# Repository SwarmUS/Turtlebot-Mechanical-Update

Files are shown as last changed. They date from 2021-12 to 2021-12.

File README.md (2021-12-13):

# Turtlebot-Mechanical-Update

This repository contains the 3D model of a modified Turtlebot Burger used by the SwarmUS project.

## Requirements
- Solidworks 2021

## Getting started

This repository contains submodule of 3D model parts. Right after cloning the project and prior to opening any assembly, run the following command:

```
git submodule update --init --recursive
```

### Repository structure

------

```
Turtlebot-Mechanical-Update
├── outputs
│   ├── dxf
|   ├── pdf
│   └── STL
|   	├── external
│   	└── internal
├── external
├── internal
├── TurtleBot
├── Turtlebot_modified.SLDASM
└── README.md
```

#### Turtlebot_modified.SLDASM

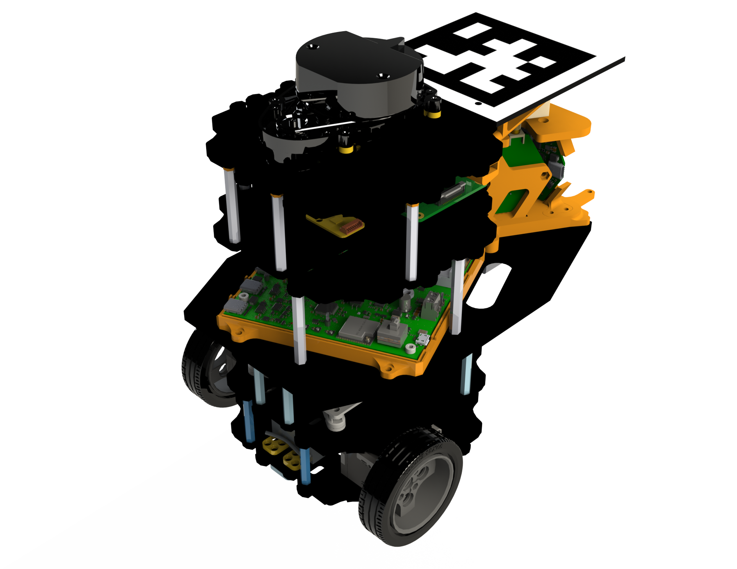
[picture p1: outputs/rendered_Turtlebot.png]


Main assembly of the modified Turtlebot. It's composed of a Turtlebot Burger with additionnal components that are external to the robot (*external*) and of components that are internal to the robot (*internal*). These components wrre mostly added to support mechanically and electrically the HiveBoard and its BeeBoards.

### Turtlebot

This folder contains all the components of the Turtlebot and it contains the Turtlebot's assembly itself. All the components and the assembly were exported from the Robotis Model on [OnShape](https://cad.onshape.com/documents/2586c4659ef3e7078e91168b/w/14abf4cb615429a14a2732cc/e/9ae9841864e78c02c4966c5e) and was converted to a SolidWorks assembly afterwards.

### external

Contains the 3D models of the external components and their supports. Significant assemblies and parts are described below:

- **qr_plate.SLDPRT**: Plate on which a QR code is glued on. Can be directly screwed on the Turtlebot top layer.
- **qr_plate_support.SLDPRT**: Supports of the qr_plate. The part has two [configurations](http://help.solidworks.com/2021/English/SolidWorks/sldworks/c_Configurations_Overview.htm), one for the port side and one for the starboard side.
- [HiveBoard-BeeBoard-Mechanical](https://github.com/SwarmUS/HiveBoard-BeeBoard-Mechanical): Submodule that contains the 3D models of the BeeBoard and the HiveBoard and their cases. 

### internal

Contains the 3D models of the internal components added to the Turtlebot. Significant assemblies and parts are described below:

- **REG_313080006.SLDPRT**: 313080006 5V regulator for powering the Hiveboard and its BeeBoards.
- **assembled_interloc_system.SLDASM**: Assembly of the HiveBoard, 3x BeeBoards, the voltage regulator (REG_313080006), a plate with the bolt pattern of all the components and some standoff for the assembly with the Turtlebot. The BeeBoards are placed in a specific pattern for interlocalisation.

### Outputs

- STL files of the custom made part in order to 3D print them.
- DXF files of the custom 2D plate. A .swg and a .pdf was generated for each .dxf files with 0.001" paths with the colorRGB(255, 0, 0) . This can be used with a laser cutting machine.

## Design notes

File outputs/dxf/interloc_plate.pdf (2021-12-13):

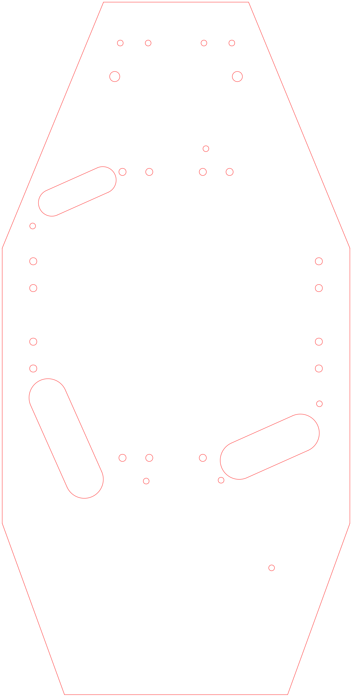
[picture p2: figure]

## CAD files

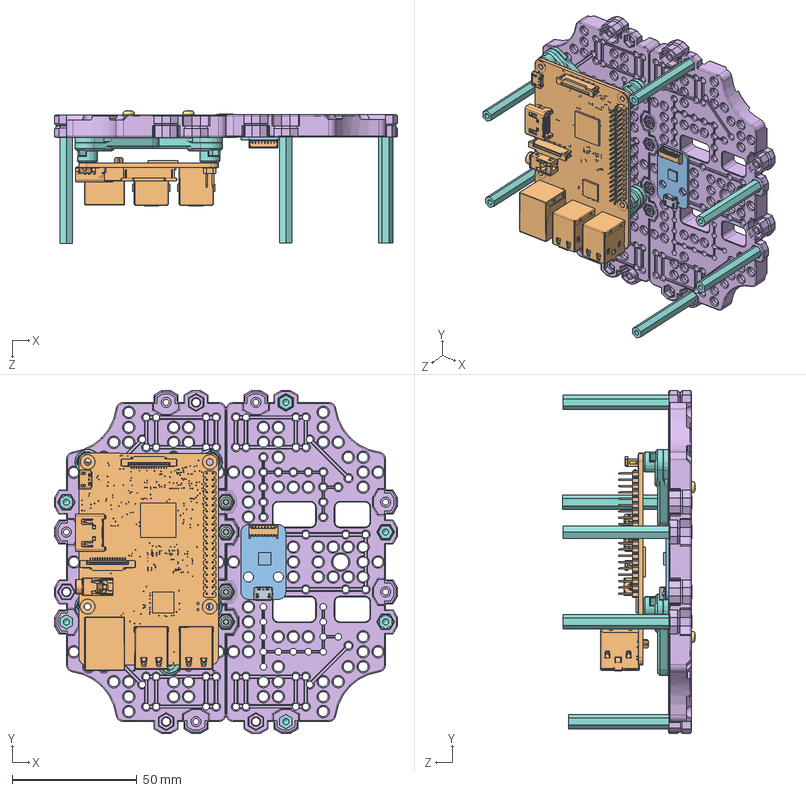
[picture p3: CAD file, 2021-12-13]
Turtlebot/Third Floor _1_.SLDASM
137.5 x 137.6 x 53.2 mm
MICRO_USB
BIC04_C01_PCB
PHS_M3X6 x 4
NUT2_M3 x 4
P-BP-A001_3D x 2
PHS_M2_5X12 x 4
PR30_IBB_01_3D x 4
Surface 18
Surface 28
Surface 36
Surface 25
Surface 34
Surface 11
Surface 24
Surface 26
Surface 33
Surface 31
Surface 1
SUPPORT_HEX_M3_0XL45_FF x 6
Surface 17
Surface 6
Surface 16
Surface 29
Surface 14
Surface 9
Surface 19
Surface 23
Surface 12
Surface 4
Surface 8
Surface 22
Surface 7
Surface 10
Surface 37
Surface 3
Surface 27
Surface 30
Surface 5
Surface 15
Surface 32
Surface 13
Surface 20
Surface 2
Surface 35
Surface 21

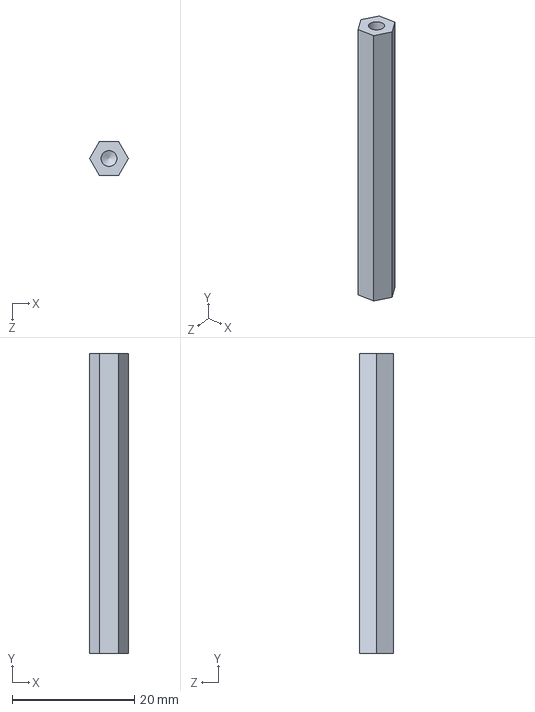
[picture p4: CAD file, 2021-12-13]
internal/m3_standoff_49mm.SLDPRT
6.35 x 49.0 x 5.50 mm

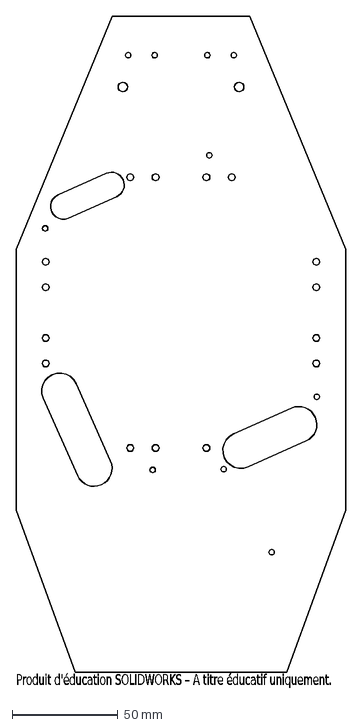
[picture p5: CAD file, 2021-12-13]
outputs/dxf/interloc_plate.DXF
Produit d'éducation SOLIDWORKS – A titre éducatif uniquement.

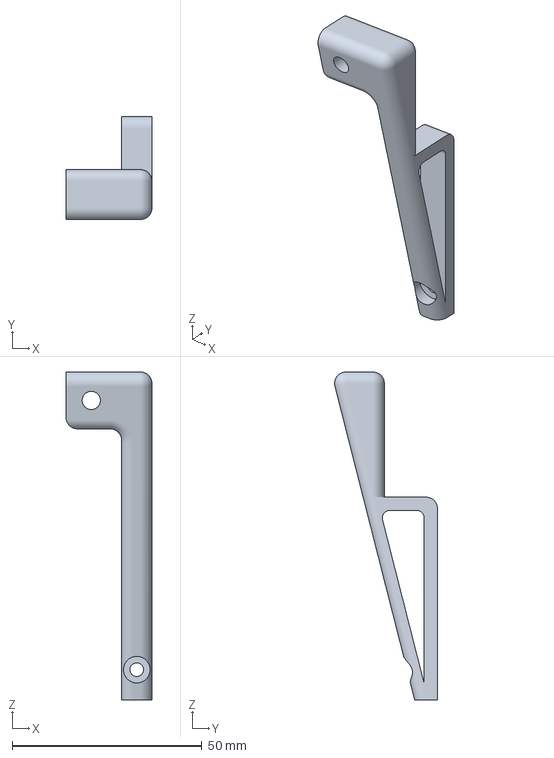
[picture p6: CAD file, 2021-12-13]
outputs/stl/qr_plate_support_miror.3MF
22.7 x 27.1 x 86.5 mm

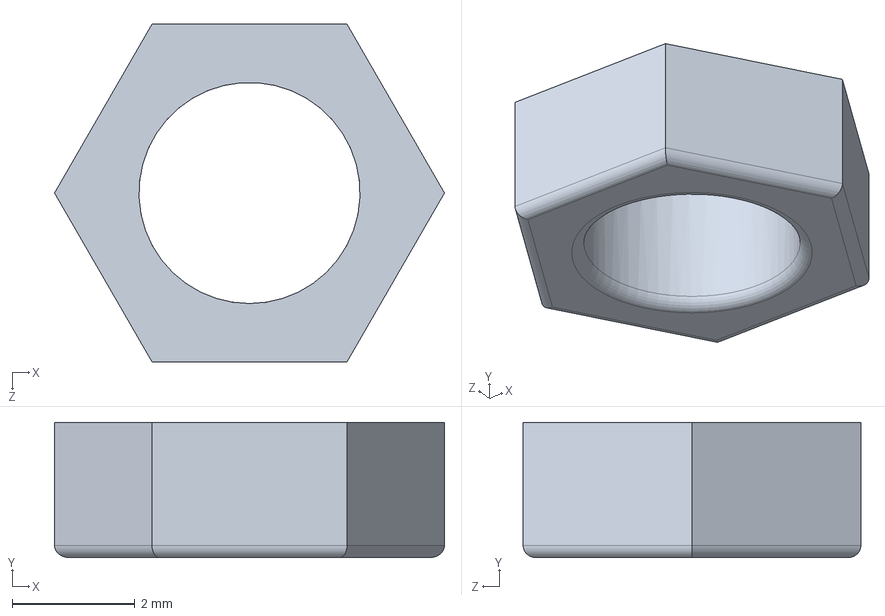
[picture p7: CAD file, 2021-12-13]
internal/hex_spacer_2_2mm.SLDPRT
6.35 x 2.20 x 5.50 mm

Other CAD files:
Turtlebot/wheel _1_.SLDASM
Turtlebot/OPENCR _1_.SLDASM
Turtlebot/connected plates _1_-3.SLDASM
Turtlebot/First Floor _1_.SLDASM
Turtlebot/Second Floor _1_.SLDASM
Turtlebot/connected plates _1_.SLDASM
Turtlebot/LDS _1_.SLDASM
Turtlebot/Forth Floor _1_.SLDASM
Turtlebot/ball_caster _1_.SLDASM
Turtlebot/wheel _2_.SLDASM
Turtlebot/USB2LDS _1_.SLDASM
Turtlebot/connected plates _1_-1.SLDASM
Turtlebot/connected plates _1_-2.SLDASM
Turtlebot/022035025.SLDPRT
Turtlebot/1-33154.SLDPRT
Turtlebot/1-33162.SLDPRT
Turtlebot/1-33193.SLDPRT
Turtlebot/1-33242.SLDPRT
Turtlebot/2-33160.SLDPRT
Turtlebot/2-33170.SLDPRT
Turtlebot/2-33199.SLDPRT
Turtlebot/2-33247.SLDPRT
Turtlebot/3-33158.SLDPRT
Turtlebot/3-33166.SLDPRT
Turtlebot/3-33196.SLDPRT
Turtlebot/3-33245.SLDPRT
Turtlebot/4-33155.SLDPRT
Turtlebot/4-33164.SLDPRT
Turtlebot/4-33194.SLDPRT
Turtlebot/4-33243.SLDPRT
Turtlebot/50MIL_HEADER_BODY-33149.SLDPRT
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

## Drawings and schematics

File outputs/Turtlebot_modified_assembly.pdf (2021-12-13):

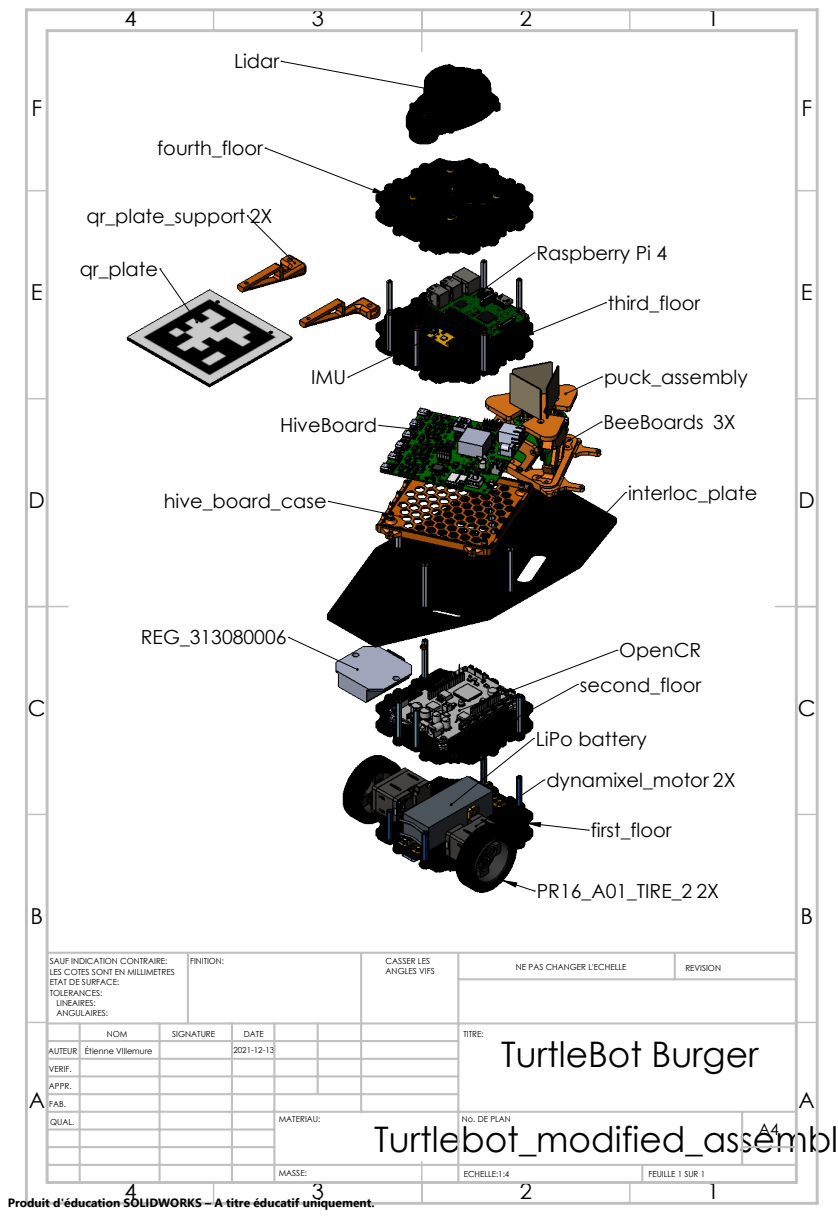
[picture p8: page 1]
qr_plate_support 2X; qr_plate; Raspberry Pi 4; LiPo battery; dynamixel_motor 2X; PR16_A01_TIRE_2 2X; BeeBoards 3X; FINITION:; CASSER LES; ANGLES VIFS; NE PAS CHANGER L'ECHELLE; REVISION; ECHELLE:1:4; FEUILLE 1 SUR 1

SAUF INDICATION CONTRAIRE:
LES COTES SONT EN MILLIMETRES
ETAT DE SURFACE:
TOLERANCES:
LINEAIRES:
ANGULAIRES:

NOM | SIGNATURE | DATE | | | | TITRE: TurtleBot Burger

AUTEUR | Étienne VIllemure | | 2021-12-13
VERIF.
APPR.
FAB.
QUAL. | | | | MATERIAU: | No. DE PLAN | A4

Produit d'éducation SOLIDWORKS – A titre éducatif uniquement.

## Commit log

2021-10-17 Interloc integration
    - Fix the the assembly of the turtlebot so its layer can be moved
    - Created a plate to hold the BeeBoards and the HiveBoard
    - Added standoff
    - Added BeeBoard and hiveboard on the plate
    - Integrated the plate as a layer of the turtlebot
    [First Floor _1_.SLDASM, Forth Floor _1_.SLDASM, LDS _1_.SLDASM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]
2021-10-17 Plate fix and spacer added
    - Added 3D printed spacer so each standoff can reach the interloc plate
    - Changed the hole size on the interloc plate used to let the electrical harness go through the layer
    [hex_spacer_2_2mm.SLDPRT, hex_spacer_2_2mm.STL, interloc_plate.SLDPRT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]
2021-10-21 Added QR code
    - Added a support to hold a QR code sheet on the top layer
    [interloc_plate.SLDPRT]
2021-10-21 Fabrication files generated
    - Generated fabrication file of the Qr plate (.DXF) , its 2x 3D printed supports (.STL) and the interloc plate (.DXF)
    [interloc_plate.DXF, interloc_plate.SLDPRT, qr_plate.DXF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]
2021-10-22 Fabrication file adjustements
    [qr_plate_support.STL, qr_plate_support_mirrored.STL]
2021-10-22 Color changes and renderering setup
    - Changed the color of the Turtlebot to reflect more the real life color of the assembly
    - Changed the color of the added plates
    - Added a camera and changed the scene to have an initial rendering setup
    - UPDATED readme with image
    [LDS _1_.SLDASM, P30_ISP_A001_3D.SLDPRT, PR16_A01_TIRE_2.SLDPRT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]
2021-10-25 Bump and adjsuted QR support
    - Bumped the HB's and BB'S cases submodule
    - Adjusted QR plate support to create a distance with the basc BeeBoard's antenna
    -Regenerated the .STL for the support
    - Fix a broken path of the supported_HiveBoard
    [qr_plate_support.STL, qr_plate_support_mirrored.STL]
2021-10-25 Reflect real life assembly
    - Moved aligned standoff between two layer
    - Added some spacer where needed
    - Increased the size of te holes of Turtlebot bolt pattern on the interloc plate to let screws pass through without threading. Threading is unnecessary in that case
    [Third Floor _1_.SLDASM, interloc_plate.SLDPRT]
2021-11-13 Updated Interloc plate with puck
    - Bump HiveBoard-BeeBoard-Mechanical to have access to the BeeBoard puck
    - Changed the configuration of the BeeBoard to a single mount of 3 BeeBoard
    - Adjusted interloc_plate (design, fabrication files)
    - Adjusted the QR support to add clearnce to the antennas ant the QR plate
    - Updated README
    [interloc_plate.DXF, interloc_plate.SLDPRT, qr_plate_support.3MF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]
2021-11-14 Balanced center of mass
    - Moved the regulator and the QR_plate at the front
    - Adjusted interloc_plate
    - Changed hole positions on the QR plate
    - Rotated the BeeBaord puck at 60 degree to remove shift the blindspot of interloc from the forward direction
    -Regenerated the plate fabrication files
    [interloc_plate.DXF, interloc_plate.SLDPRT]
